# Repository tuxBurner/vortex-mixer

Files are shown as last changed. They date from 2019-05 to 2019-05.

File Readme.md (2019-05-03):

# Vortex Paint Mixer

This is my OpenSource vortex paint mixer.

You can also find it on thingiverse: https://www.thingiverse.com/thing:3605287

The reason why i created this, is i wanted to have an easy way to shake my paints. I used an adapter on a jig saw, which worked pretty well but was verry noisy to.

I stumpled over the vortex mixer from NDubiel on thingiverse: https://www.thingiverse.com/thing:534894 which was quite good but i wanted to improve some stuff.

Look the video how it works

Vortex Mixer in Action (http://www.youtube.com/watch?v=J79AnS1BsYA "Vortex Mixer in Action")

## Contribute

When you found a bug or have enhancement feel free to create a pull request or an issue :)

## Software used to create this project

* For 3d modelling: [http://openscad.org](http://openscad.org)
* For the pcb: [http://http://kicad-pcb.org/](http://kicad-pcb.org/)

I thank all the people which make it possible to create a project like this with there free software.

## Scad files

The case / lid and motorclamp scad file is the [scadfiles/case.scad](scadfiles/case.scad)

The top scad file is the [scadfiles/top.scad](scadfiles/top.scad)

## Howto build the mixer

### Tools

  * A 3d printer or use one of the services which print the objects for you
  * Soldering iron
  * Superglue
  * Hotglue gun
  * Optional if you want to create the pcb a mill or edging equipment

### Motorcontroller PCB Components

  * 1 x Diode (for example a 4007)
  * 1 x Poti 10K
  * 2 x Capacitor 47uF at 20V or greater 
  * 1 x LM317
  * 1 x Heatsink for the LM317 **required** 
  * 1 x 1k Resistor
  * 2 x Screw Terminal (Optional) 

### Other electronic Components

  * 12V DC Motor
  * Micro Switch
  * 1 x Powerplug (Optional) 
  * Poti Knob
  * 12 to 20 volt power supply

### General Components

  * 4 x Rubber Foot 
  * 1 x M3 * 30 Bolt + 3M Nut for the motor clamp
  * 5 x M3 tapping screws
  * Bearing for the cuppler
  * For the top 4M x 20 Bolt and 2 4M x Nuts

### Components to print

#### For the Mixer Case:

Print the following parts. Each one time.

I used 20% infill and PLA.

* [stls/case_bottom.stl](stls/case_bottom.stl)
* [stls/motor_clamp.stl](stls/motor_clamp.stl)
* [stls/wedge.stl](stls/wedge.stl)
* [stls/lid.stl](stls/lid.stl)
* [stls/coupler.stl](stls/coupler.stl)

#### For the paint bottle tops

Select the one which yo need.

I used 20% infill and PLA.

* [Vallejo](stls/tops/vallejo_top.stl)
* [Vallejo big bottle](stls/tops/vallejo_big_top.stl)
* [Games Workshop](stls/tops/games_workshop_top.stl)
* [Games Workshop old](stls/tops/games_workshop_old_top.stl)

## Motorcontroller PCB

The schemantics is like this

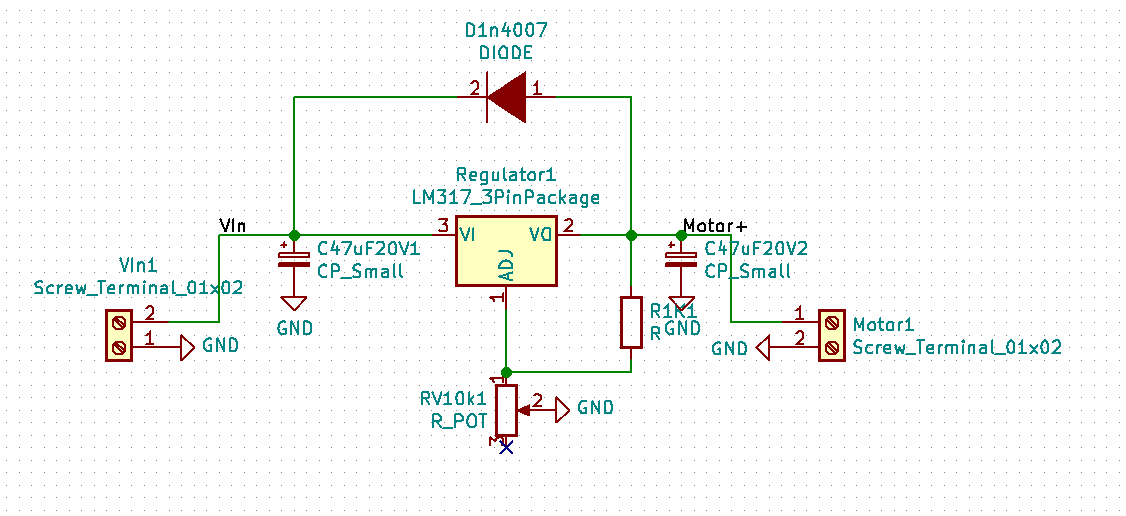
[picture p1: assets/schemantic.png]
PCB schemantic


You can either use the pcb which i generated with KICAD. The project files are located in the folder: **[pcb](pcb)**

If you don't have the possibility to create the pcb you can also freewire the electronics.

## Build Instructions

### Mixer

Hot glue the micro switch into the case and wire the switch to the power plug.







Put the motorclamp and the motor together


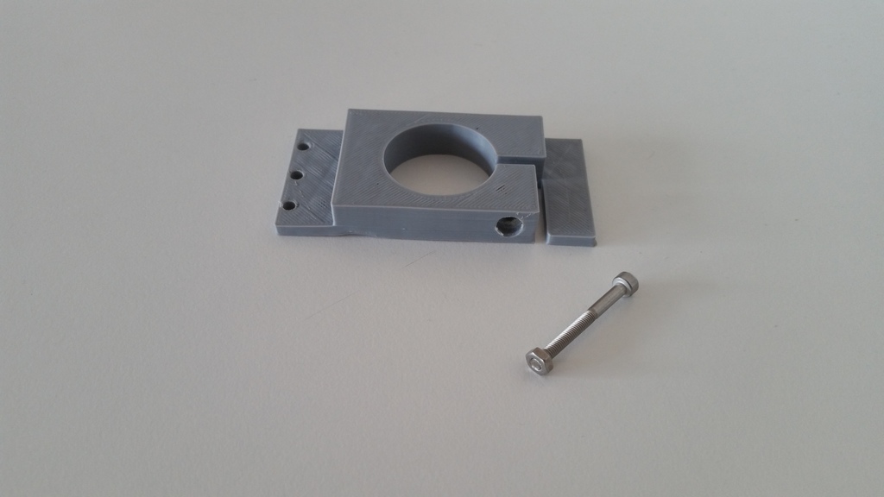
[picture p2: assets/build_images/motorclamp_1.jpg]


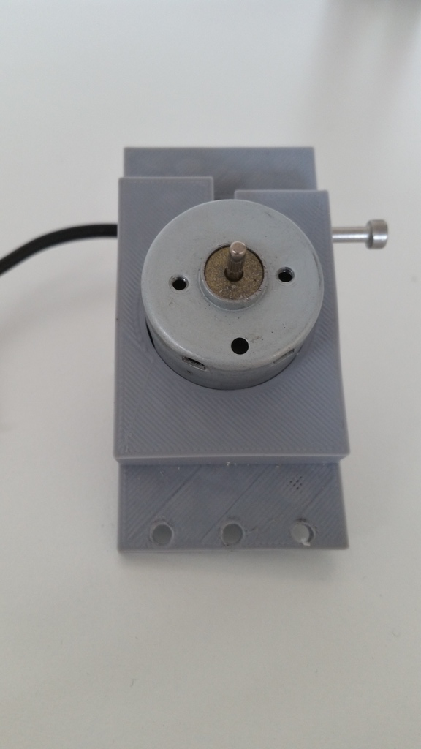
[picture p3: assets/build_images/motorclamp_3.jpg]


Assemble the pcb. Don't forget the heatsink :)



Wire the wires to the pcb from the powerplug, micro switch and the motor.



Fix the poti with the nut onto the case.

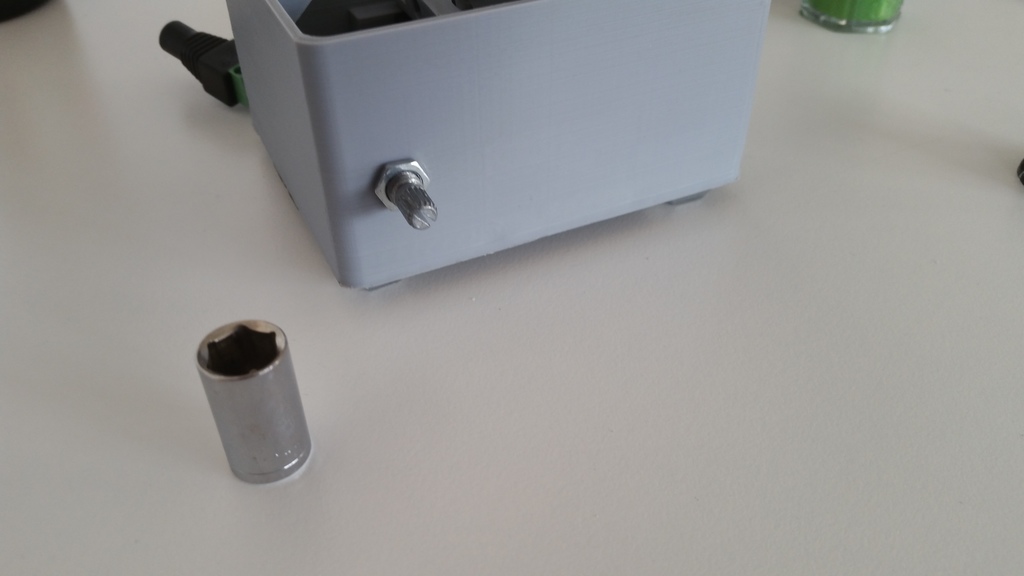
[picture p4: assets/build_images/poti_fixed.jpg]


Add the knob to the poti.

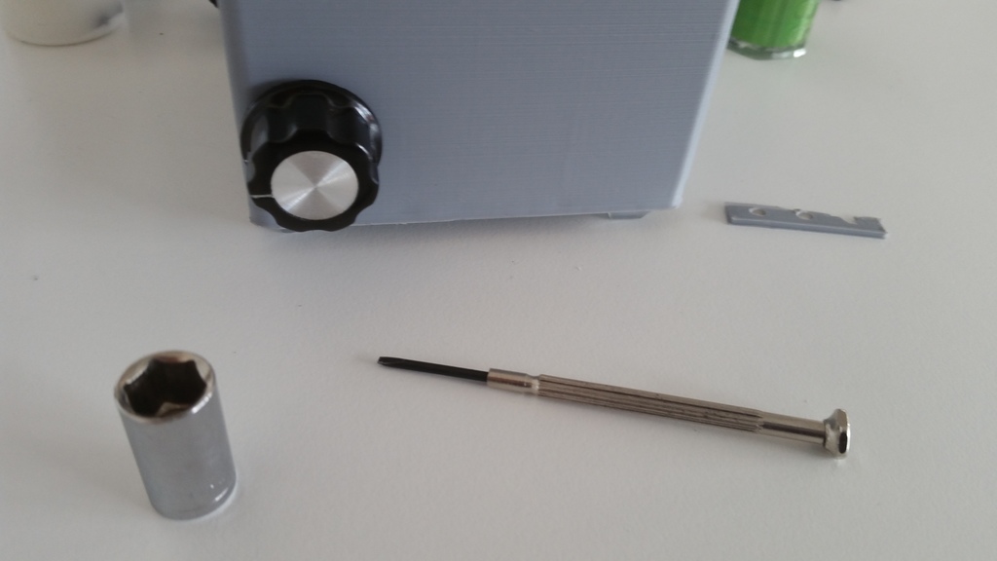
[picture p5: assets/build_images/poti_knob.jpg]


Add the wedge to the motor clamp. Mine broke a little bit when i tokked of the printer. But it is still working. 

¯\\_(ツ)_/¯

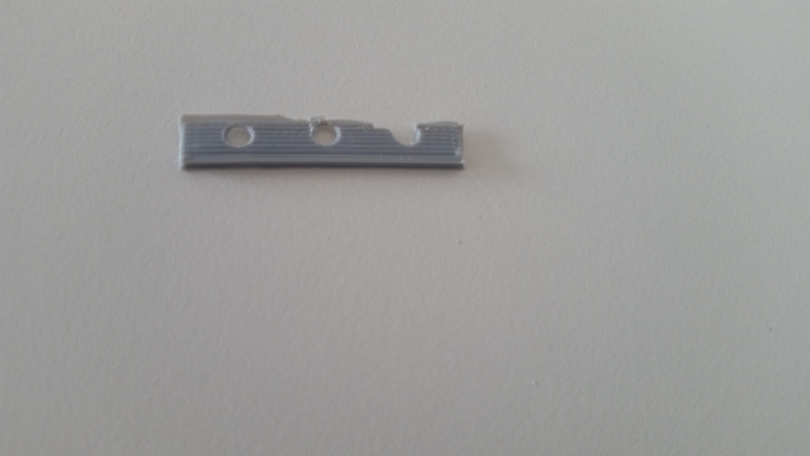
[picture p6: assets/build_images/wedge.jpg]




Screw the motorclamp into the case.



Screw the lid onto the case.



Superglue the bearing into the coupler.

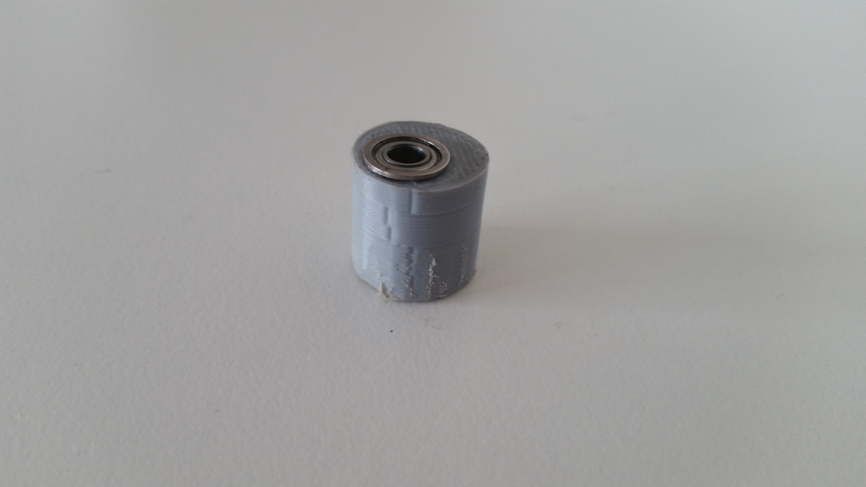
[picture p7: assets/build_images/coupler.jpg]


Put the coupler onto the motor.



## Paint bottle top

Here is a picture of the diffrent tops and the corresponding paint bottles.



Put a M4 nut into the bottom of the top.

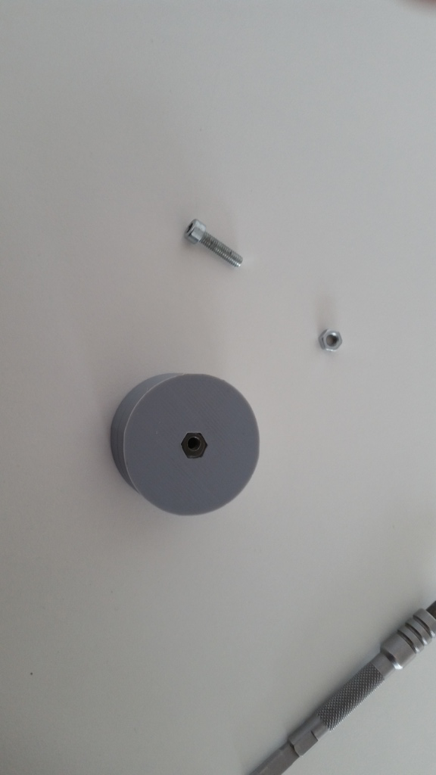
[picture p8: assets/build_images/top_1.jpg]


Screw a M4 bolt from the other side into the top and put a second M4 nut at the bottom. 

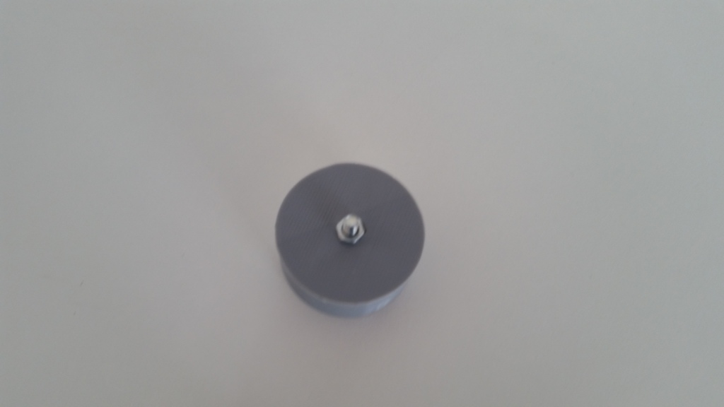
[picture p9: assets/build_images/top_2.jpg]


**DONE ! :)**

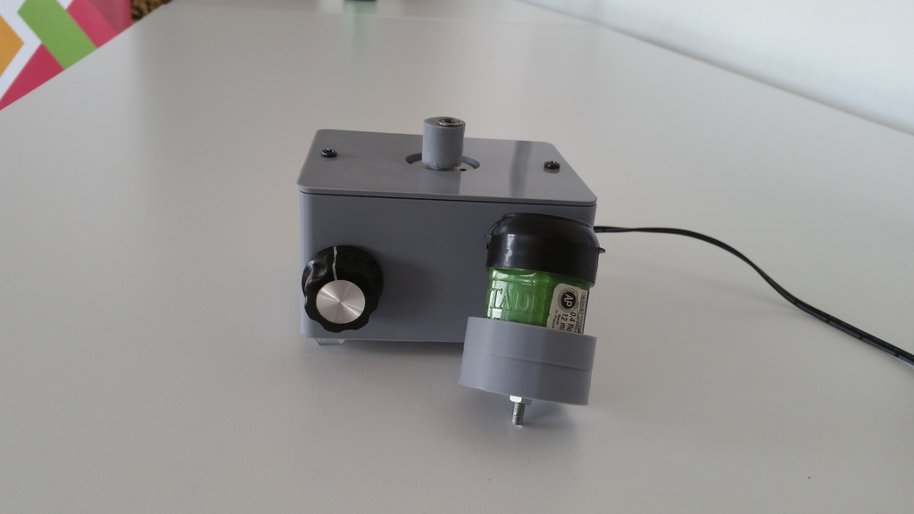
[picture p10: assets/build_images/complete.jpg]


Just plugin the power and push down the color top into the coupler.

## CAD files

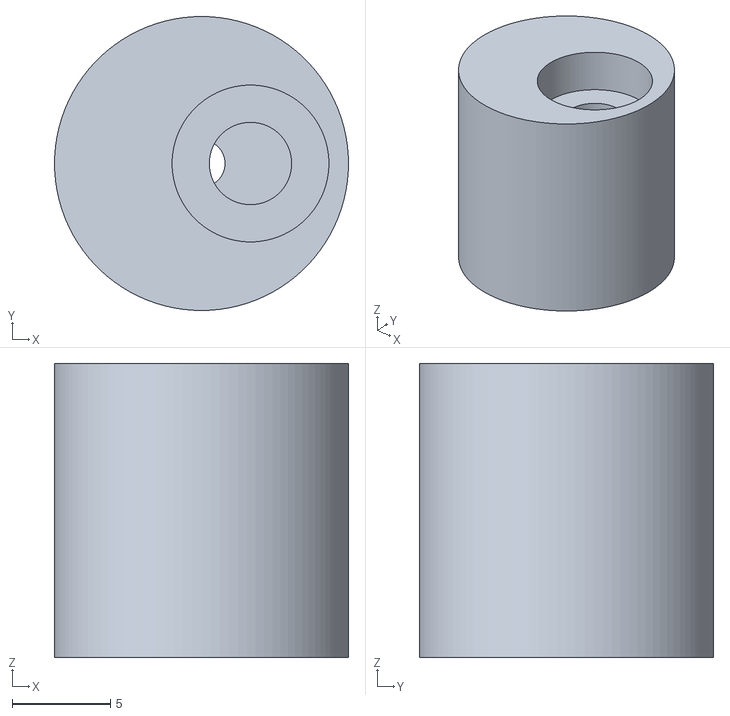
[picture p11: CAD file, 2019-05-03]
stls/coupler.stl
15.0 x 15.0 x 15.0

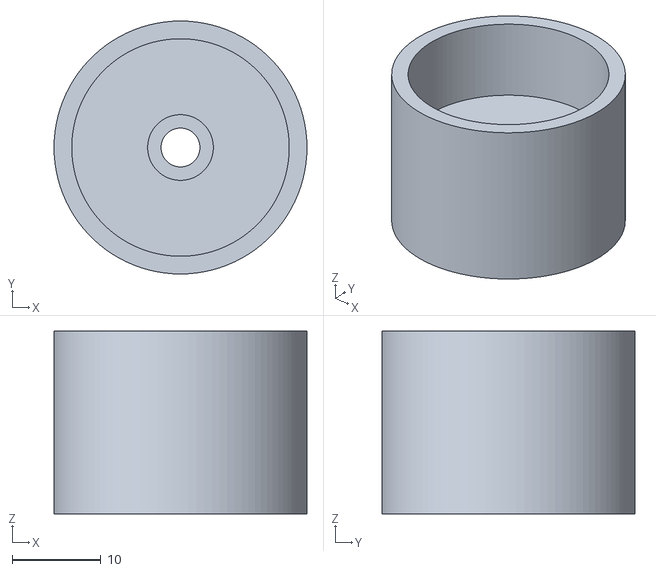
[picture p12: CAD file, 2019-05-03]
stls/tops/vallejo_top.stl
28.5 x 28.5 x 20.6

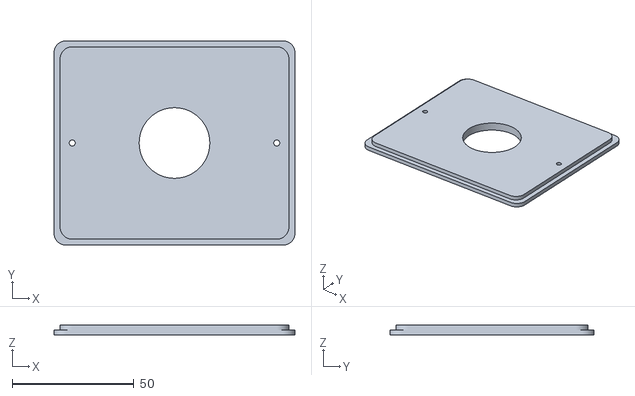
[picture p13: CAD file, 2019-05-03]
stls/lid.stl
99.0 x 84.0 x 4.00

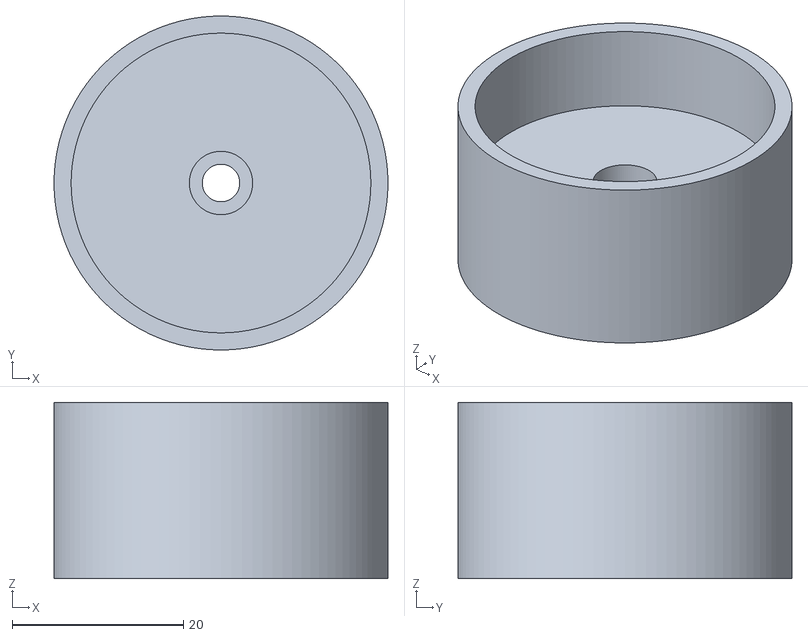
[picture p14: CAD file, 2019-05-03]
stls/tops/vallejo_big_top.stl
39.0 x 39.0 x 20.6

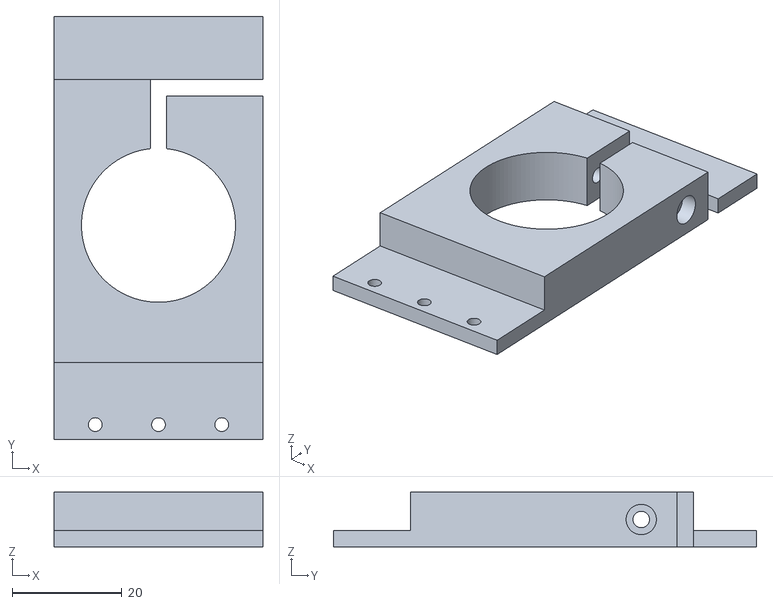
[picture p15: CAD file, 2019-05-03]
stls/motor_clamp.stl
38.0 x 77.0 x 10.0

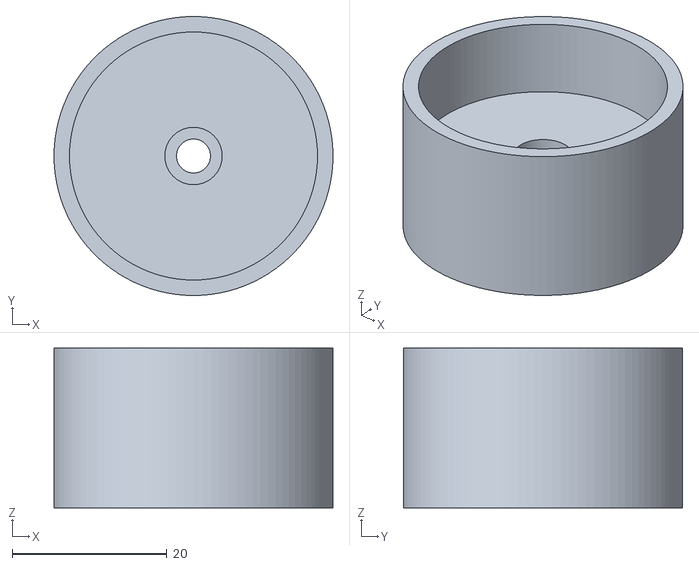
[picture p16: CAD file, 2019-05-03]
stls/tops/games_workshop_top.stl
36.0 x 36.0 x 20.6

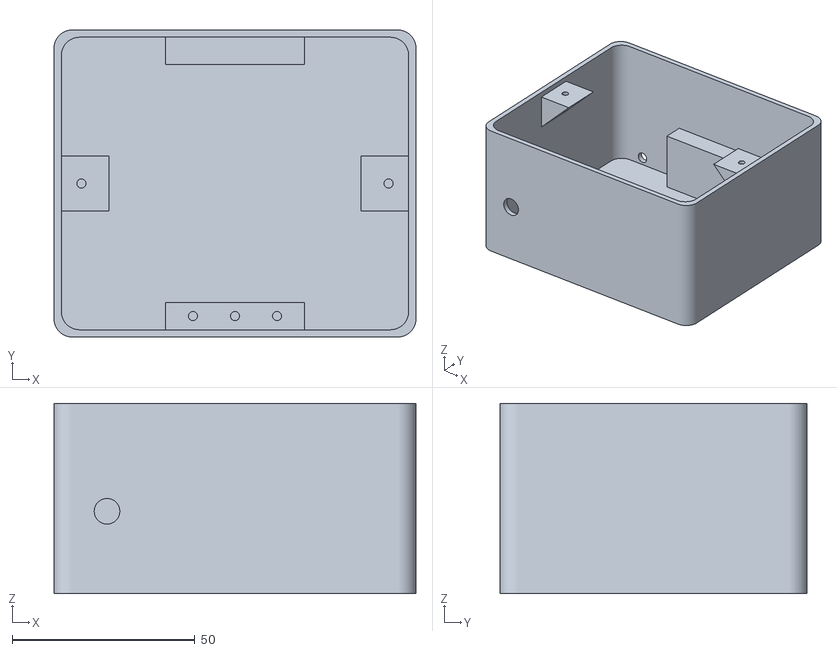
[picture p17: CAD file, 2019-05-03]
stls/case_bottom.stl
99.0 x 84.0 x 52.0

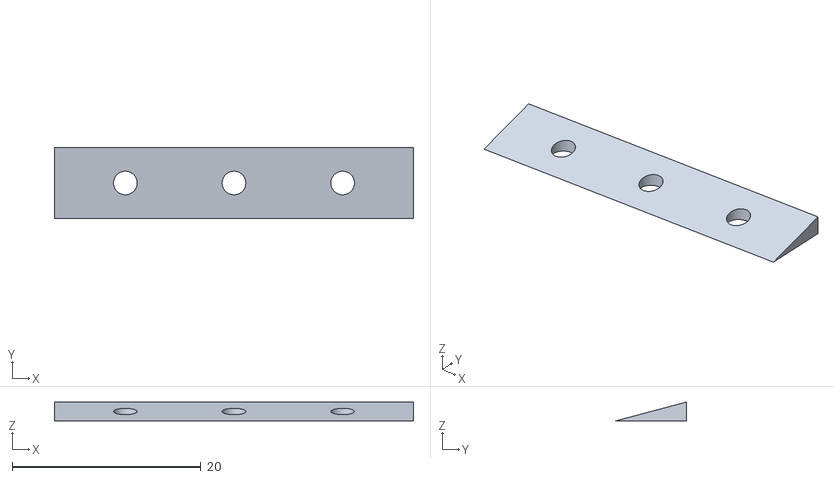
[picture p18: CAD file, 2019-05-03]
stls/wedge.stl
38.0 x 7.50 x 2.00

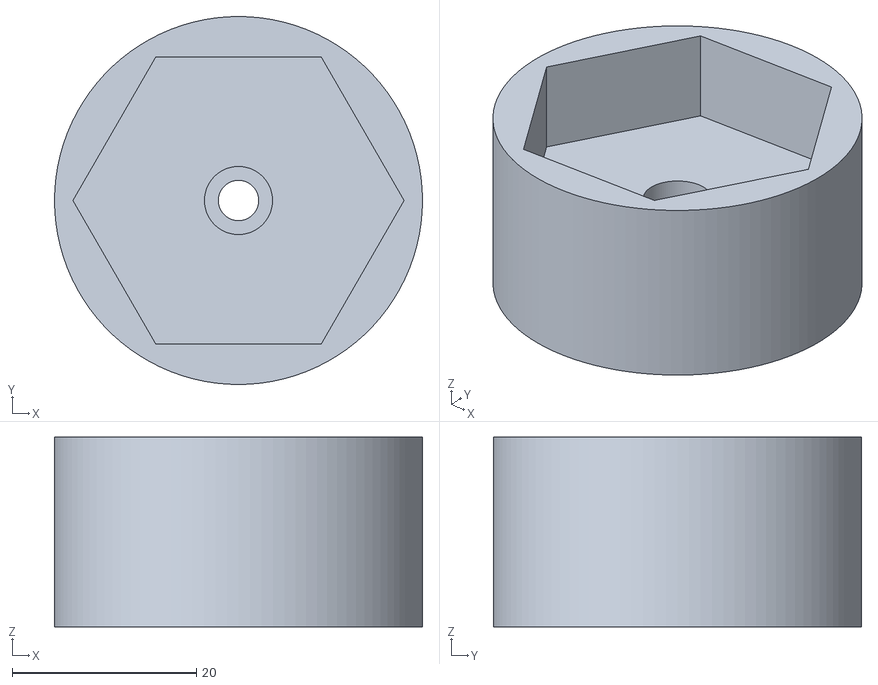
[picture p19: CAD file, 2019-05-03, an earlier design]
stls/tops/games_workshop_old_top.stl
40.0 x 40.0 x 20.6

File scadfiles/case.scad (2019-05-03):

use <boxes.scad>
include <nuts_and_bolts.scad>

/**
* Motor dimensions
*/
motorDia=28;
motorHeight=50;
motorShaftDia=3;
motorShaftLength=5;

/**
* Case dimensions
*/
caseWidth=95;
caseDepth=80;
caseHeight=motorHeight;
caseCornerRadius=5;

// thickness of the wall of the case
caseWallThickness=2;

/**
* Calculate the case real dimensions
*/
outerCaseWidth = caseWidth+2*caseWallThickness;
outerCaseDepth = caseDepth+2*caseWallThickness;
outerCaseHeight = caseHeight+caseWallThickness;

/**
* Case Lid dimensions
*/
caseLidLidHeight=2;
caseLidHeight=caseLidLidHeight*2;
caseLidTolerance=1;
caseLidScrewDia=2.5;

/**
* Prim for fixiatet the lid to the case
*/
caseLidFixPrismWidth=15;
caseLidFixPrismDepth=15;
caseLidFixPrismHeight=15;

/**
* Motor clamp dimensions
*/
motorClampHeight=10;
motorClampFlesh=5;
motorClampWidth=motorClampFlesh * 2 + motorDia;
motorClampLength = caseDepth - 2;
motorClampBoltSize=3;
motorClampNutHeight=motorClampWidth / 5;
motorClampTolerance=3;
motorClampLidLength=caseDepth / 8;
motorClampFixHeight=3;
motorClampFixWidth=15;
motorClampFixTolerance=1;
motorClampWedgeHeight=2;

motorClampCaseFixHeight =  caseHeight / 2;
motorClampCaseFixDepth = motorClampFixWidth / 2;

/**
* Motor clamp variables where to put the screws for the motorclamp and the case
*/
motorClampFixScrewDia = 2.5;
motorClampFixScrewHeight = 10;
motorClampFixScrewTolerance = 5 + motorClampFixScrewDia;
motorClampFixScrewPositions=[
  [motorClampFixScrewTolerance, motorClampCaseFixDepth / 2],
  [motorClampWidth / 2, motorClampCaseFixDepth / 2],
  [motorClampWidth - motorClampFixScrewTolerance, motorClampCaseFixDepth / 2],
];

/**
* Dimensions where to put the micro switch at
*/
microSwitchCaseFixHeight = motorClampCaseFixHeight - 2;
microSwitchCaseFixDepth = motorClampCaseFixDepth;


/**
* For debug purpose the pcb 
*/
pcbXTollerance=1;
pcbWidth=24;
pcbDepth=33;
pcbHeight=24;

/**
* Poti dimensions
*/
potiHoleDia=7;
potiHoleXOffset=8;
potiHolezOffset=17;

/**
* Diameter for the power cable
*/
cableHoleDia=4;

/**
* Coupler dimensions
*/
couplerDia=15;
couplerHeight=15;
couplerScrewDia=4.2;
couplerBearingDia=8;
couplerBearingHeight=3;
couplerMoterShaftDia=2.4;
couplerBearingOffset=2.5;


$fn=100;


$previewMotor=false;
$debugLid=false;
$debugMotorClamp=false;



/**
* Generates the bottom of the case
*/
module bottomCase() {  
  union() {
    translate([outerCaseWidth / 2, outerCaseDepth / 2, outerCaseHeight / 2]) {
      difference() {  
        roundedBox([outerCaseWidth, outerCaseDepth, outerCaseHeight], caseCornerRadius, true);
        translate([0, 0, caseWallThickness]) {
          roundedBox([caseWidth, caseDepth, caseHeight], caseCornerRadius, true);
        }
      }
    }

    translate([0, 0, outerCaseHeight -caseLidFixPrismHeight-caseLidLidHeight]) {
      translate([0, (outerCaseDepth - caseLidFixPrismWidth) / 2, 0]) {
        lidHolder(caseLidFixPrismWidth, caseLidFixPrismHeight, caseLidFixPrismDepth);  
      }
      translate([outerCaseWidth , (outerCaseDepth + caseLidFixPrismWidth) / 2, 0]) {
        rotate([0, 0, 180]) {      
          lidHolder(caseLidFixPrismWidth, caseLidFixPrismHeight, caseLidFixPrismDepth);  
        }
      }
      translate([(outerCaseWidth + caseLidFixPrismWidth) / 2 ,0, 0]) {
        rotate([0, 0, 90]) {      
         // #lidHolder(caseLidFixPrismWidth, caseLidFixPrismHeight, caseLidFixPrismDepth);  
        }
      }
      translate([(outerCaseWidth - caseLidFixPrismWidth) / 2 ,outerCaseDepth, 0]) {
        rotate([0, 0, -90]) {      
          //lidHolder(caseLidFixPrismWidth, caseLidFixPrismHeight, caseLidFixPrismDepth);  
        }
      }
    }
  
    translate([(outerCaseWidth - motorClampWidth) / 2 , caseWallThickness,caseWallThickness]) {    
      motorClampCaseFixiation();    
      translate([0,caseDepth - microSwitchCaseFixDepth, 0]) {
        microSwitchHolder();  
      }
    }
  }
}

/**
* Draws the motor clamp
*/
module motorClamp() {
  color("DarkKhaki") {
    difference() {
      cube(size=[motorClampWidth, motorClampLength, motorClampHeight], center=false);
      
      // cut out the fixiation which is thinner so we can bend it down
      translate([0, 0, motorClampFixHeight]) {
        cube(size=[motorClampWidth, motorClampFixWidth,motorClampHeight- motorClampFixHeight], center=false);  
      }

      // cut off the tolerance      
      cube(size=[motorClampWidth, motorClampFixTolerance, motorClampFixHeight], center=false);
      

      // cut out the screwholes
      clampScrewHoles(motorClampFixHeight);
   
      // cut out the motor
      translate([motorClampWidth / 2, caseDepth / 2, 0]) {
        cylinder(d=motorDia, h=motorClampHeight, center=false);  
      }

      // cut out the tolerance slit 
      motorClampLidOffset = (caseDepth + motorDia) / 2 -0.5;
      translate([(motorClampWidth - motorClampTolerance) / 2,motorClampLidOffset , 0]) {
        cube(size=[motorClampTolerance, motorClampLidLength, motorClampHeight], center=false);  
        translate([0, motorClampLidLength, 0]) {
          cube(size=[motorClampWidth - motorClampTolerance, motorClampTolerance, motorClampHeight], center=false);  
        }
      } 
      
      // add the hole for the fixiation screw
      translate([motorClampWidth - motorClampBoltSize , (motorClampLength - motorClampBoltSize * 2 - (motorClampLength / 2 - motorDia / 2 - motorClampLidLength)), motorClampHeight  / 2]) { 
        rotate([0, 270, 0]) {
          boltHole(motorClampBoltSize, length= motorClampWidth-motorClampBoltSize, proj=-1);  
        }        
      } 

      // add a nut hole 
      translate([motorClampNutHeight, (motorClampLength - motorClampBoltSize * 2 - (motorClampLength / 2 - motorDia / 2 - motorClampLidLength)), motorClampHeight  / 2]) {         
        rotate([0, 270, 0]) {
          cylinder(r= METRIC_NUT_AC_WIDTHS[motorClampBoltSize]/2+0.5, h=motorClampNutHeight, $fn = 6, center=[0,0]);
        }
      }

      // slim the end of the clamp 
      backCutOffOffset = motorClampLidOffset + motorClampLidLength + motorClampTolerance;
      translate([0, backCutOffOffset, motorClampFixHeight]) {
        cube(size=[motorClampWidth, motorClampLength - backCutOffOffset, motorClampHeight- motorClampFixHeight], center=false);
      }
    }
  }
}

/**
* Cut out the screwholes for fix the clamp
*/ 
module clampScrewHoles(holesHeight) {
  for(screwPos = motorClampFixScrewPositions) {
    translate([screwPos[0], screwPos[1], 0]) {
      cylinder(d=motorClampFixScrewDia, h=holesHeight, center=false);  
    }
  }
}

/**
* Draws the clamp case motor fixiation
*/
module motorClampCaseFixiation() {
  color("Teal") {
    difference() {
      cube(size=[motorClampWidth, motorClampCaseFixDepth, motorClampCaseFixHeight], center=false);
      translate([0, 0, motorClampCaseFixHeight - motorClampFixScrewHeight]) {
        clampScrewHoles(motorClampFixScrewHeight); 
      }    
    }
  }
}

/**
* Draws the holder for the microswitch
*/
module microSwitchHolder() {
  color("Gainsboro") {
    difference() {
      cube(size=[motorClampWidth, microSwitchCaseFixDepth, microSwitchCaseFixHeight], center=false);      
    }
  }
}

/**
* Draws the lid
*/
module lid() {
  translate([outerCaseWidth / 2, outerCaseDepth / 2, 0]) {
    difference() {
      union() {
        roundedBox([outerCaseWidth, outerCaseDepth, caseLidHeight - caseLidLidHeight], caseCornerRadius, true);
        translate([0, 0, caseLidLidHeight]) {
          roundedBox([caseWidth - caseLidTolerance, caseDepth- caseLidTolerance, caseLidLidHeight], caseCornerRadius, true);
        }
      }
  
      translate([0, 0, -1 * (caseLidLidHeight / 2)]) {
        cylinder(d=motorDia + caseLidTolerance, h=caseLidHeight, center=false);  
        
        translate([(outerCaseWidth - caseLidFixPrismDepth) / 2, 0, 0]) {
          cylinder(d=caseLidScrewDia, h=caseLidHeight, center=false);  
        }

        translate([-1*(outerCaseWidth - caseLidFixPrismDepth) / 2, 0, 0]) {
          cylinder(d=caseLidScrewDia, h=caseLidHeight, center=false);  
        }

        translate([0,-1*(outerCaseDepth - caseLidFixPrismDepth) / 2, 0]) {
         // cylinder(d=caseLidScrewDia, h=caseLidHeight, center=false);  
        }

        translate([0,(outerCaseDepth - caseLidFixPrismDepth) / 2, 0]) {
          //cylinder(d=caseLidScrewDia, h=caseLidHeight, center=false);  
        }
        
      }
    }
  }
}

/**
* In preview mode this is drawn to check if the pcb fits into the case
*/
module pcbPreview() {
  color("Red") {
    translate([caseWallThickness + pcbXTollerance, caseWallThickness, caseWallThickness]) {
     cube(size=[pcbWidth, pcbDepth, pcbHeight], center=false);   
    }    
  }
}
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

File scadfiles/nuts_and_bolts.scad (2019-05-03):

// Copyright 2010 D1plo1d

// This library is dual licensed under the GPL 3.0 and the GNU Lesser General Public License as per http://creativecommons.org/licenses/LGPL/2.1/ .

//testNutsAndBolts();

module SKIPtestNutsAndBolts()
{
	$fn = 360;
	translate([0,15])nutHole(3, proj=2);
	boltHole(3, length= 30, proj=2);
}

MM = "mm";
INCH = "inch"; //Not yet supported

//Based on: http://www.roymech.co.uk/Useful_Tables/Screws/Hex_Screws.htm
METRIC_NUT_AC_WIDTHS =
[
	-1, //0 index is not used but reduces computation
	-1,
	4.38,//m2
	6.40,//m3
	8.10,//m4
	9.20,//m5
	11.50,//m6
	-1,
	15.00,//m8
	-1,
	19.60,//m10
	-1,
	22.10,//m12
	-1,
	-1,
	-1,
	27.70,//m16
	-1,
	-1,
	-1,
	34.60,//m20
	-1,
	-1,
	-1,
	41.60,//m24
	-1,
	-1,
	-1,
	-1,
	-1,
	53.1,//m30
	-1,
	-1,
	-1,
	-1,
	-1,
	63.5//m36
];
METRIC_NUT_THICKNESS =
[
	-1, //0 index is not used but reduces computation
	-1,
	1.6,//m2
	2.40,//m3
	3.20,//m4
	4.00,//m5
	5.00,//m6
	-1,
	6.50,//m8
	-1,
	8.00,//m10
	-1,
	10.00,//m12
	-1,
	-1,
	-1,
	13.00,//m16
	-1,
	-1,
	-1,
	16.00//m20
	-1,
	-1,
	-1,
	19.00,//m24
	-1,
	-1,
	-1,
	-1,
	-1,
	24.00,//m30
	-1,
	-1,
	-1,
	-1,
	-1,
	29.00//m36
];

COURSE_METRIC_BOLT_MAJOR_THREAD_DIAMETERS =
[//based on max values
	-1, //0 index is not used but reduces computation
	-1,
	1.6,//m2
	2.98,//m3
	3.978,//m4
	4.976,//m5
	5.974,//m6
	-1,
	7.972,//m8
	-1,
	9.968,//m10
	-1,
	11.966,//m12
	-1,
	-1,
	-1,
	15.962,//m16
	-1,
	-1,
	-1,
	19.958,//m20
	-1,
	-1,
	-1,
	23.952,//m24
	-1,
	-1,
	-1,
	-1,
	-1,
	29.947,//m30
	-1,
	-1,
	-1,
	-1,
	-1,
	35.940//m36
];

//Based on: http://www.roymech.co.uk/Useful_Tables/Screws/cap_screws.htm
METRIC_BOLT_CAP_DIAMETERS =
[
	-1, //0 index is not used but reduces computation
	-1,
	-1,
	5.50,//m3
	7.00,//m4
	8.50,//m5
	10.00,//m6
	-1,
	13.00,//m8
	-1,
	16.00,//m10
	-1,
	18.00,//m12
	-1,
	-1,
	-1,
	24.00,//m16
	-1,
	-1,
	-1,
	30.00//m20
	-1,
	-1,
	-1,
	36.00,//m24
	-1,
	-1,
	-1,
	-1,
	-1,
	45.00,//m30
	-1,
	-1,
	-1,
	-1,
	-1,
	54.00//m36
];

module nutHole(size, units=MM, tolerance = +0.0001, proj = -1)
{
	//takes a metric screw/nut size and looksup nut dimensions
	radius = METRIC_NUT_AC_WIDTHS[size]/2+tolerance;
	height = METRIC_NUT_THICKNESS[size]+tolerance;
	if (proj == -1)
	{
		cylinder(r= radius, h=height, $fn = 6, center=[0,0]);
	}
	if (proj == 1)
	{
		circle(r= radius, $fn = 6);
	}
	if (proj == 2)
	{
		translate([-radius/2, 0])
			square([radius*2, height]);
	}
}

module boltHole(size, units=MM, length, tolerance = +0.0001, proj = -1)
{
	radius = COURSE_METRIC_BOLT_MAJOR_THREAD_DIAMETERS[size]/2+tolerance;
	capHeight = size+tolerance;
	capRadius = METRIC_BOLT_CAP_DIAMETERS[size]/2+tolerance;

	if (proj == -1)
	{
	translate([0, 0, -capHeight])
		cylinder(r= capRadius, h=capHeight);
	cylinder(r = radius, h = length);
	}
	if (proj == 1)
	{
		circle(r = radius);
	}
	if (proj == 2)
	{
		translate([-capRadius/2, -capHeight])
			square([capRadius*2, capHeight]);
		square([radius*2, length]);
	}
}

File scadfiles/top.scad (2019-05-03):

include <nuts_and_bolts.scad>

/**
* Size of the bolts
*/
boltSize=4;
boltTolerance=0.2;
boltFlesh=3;

bottomHeight = boltSize + boltTolerance + boltFlesh + METRIC_NUT_THICKNESS[boltSize] + boltTolerance;

wallThickness=2;

$fn=100;

/**
* Top configurations
*/
topConfigurations = [
  [10, 24.5], // normal vallejo top
  [10, 35], // vallejo big top
  [10,32], // games workshop 
  [10,36,6] // games workshop old
];



/**
* Module for creating a top
*/
module top(height, dia, fn=100) {
  
  union() {
    difference() {
      cylinder(d=dia+2*wallThickness, h=bottomHeight, center=false);
      translate([0, 0, bottomHeight - boltSize - boltTolerance]) {
        rotate([0, 180, 0]) {
          #boltHole(size=boltSize,length=bottomHeight, tolerance=boltTolerance);  
        }  
      }
      nutHole(size=boltSize,tolerance=boltTolerance);    
    }
  
    translate([0, 0, bottomHeight]) {
      difference() {
        cylinder(d=dia+2*wallThickness, h=height, center=false);
        cylinder(d=dia, h=height, center=false,$fn=fn);
      }
    }
  }
}


/**
* Iterate over the tops and draw them
*/
for(idx = [0:len(topConfigurations)-1])  {  
  xOffset = sumv(topConfigurations,idx,0);
  translate([xOffset,0,0]) {
    fn = (len(topConfigurations[idx]) == 2) ? 100 : topConfigurations[idx][2];     
    top(height = topConfigurations[idx][0], dia = topConfigurations[idx][1], fn = fn);
  }
}

/**
* Used to calculate the sum of all dias from to
*/
function sumv(v,i,s=0) = (i==s ? v[i][1]+10 : v[i][1]+10 + sumv(v,i-1,s));

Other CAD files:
scadfiles/boxes.scad

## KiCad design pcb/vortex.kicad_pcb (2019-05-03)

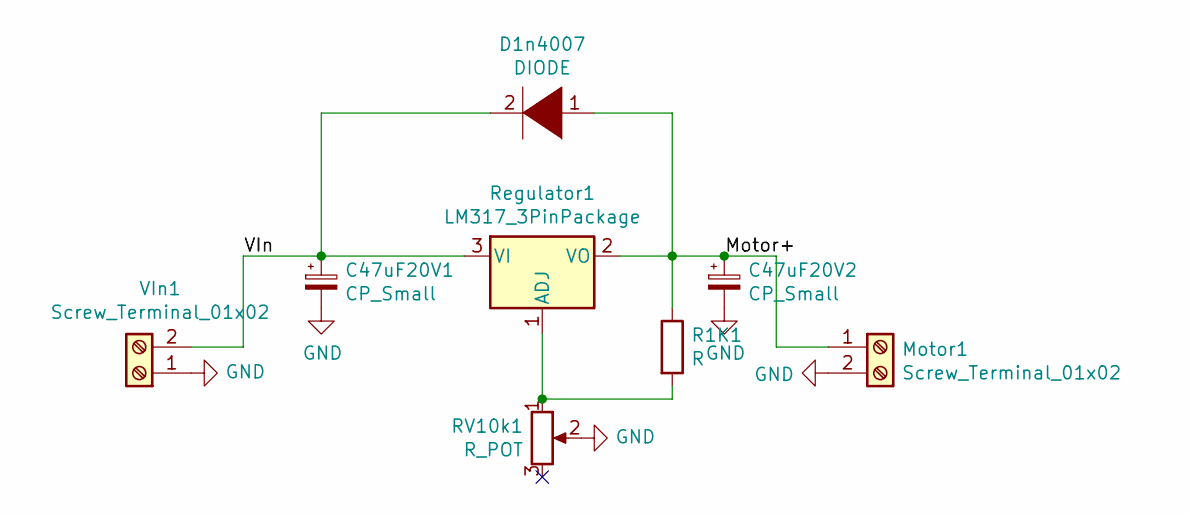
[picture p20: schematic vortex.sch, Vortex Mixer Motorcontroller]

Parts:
C47uF20V1, C47uF20V2: CP_Small; CP_Radial_D5.0mm_P2.50mm
D1n4007: DIODE; D_A-405_P7.62mm_Horizontal
Motor1: Screw_Terminal_01x02; TerminalBlock_bornier-2_P5.08mm
R1K1: R; R_Axial_DIN0207_L6.3mm_D2.5mm_P7.62mm_Horizontal
RV10k1: R_POT; Potentiometer_Alps_RK163_Single_Horizontal
Regulator1: LM317_3PinPackage; TO-220-3_Vertical
VIn1: Screw_Terminal_01x02; TerminalBlock_bornier-2_P5.08mm

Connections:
/Motor+: C47uF20V2.1, D1n4007.1 (K), Motor1.1, R1K1.1, Regulator1.2 (VO)
/VIn: C47uF20V1.1, D1n4007.2 (A), Regulator1.3 (VI), VIn1.2
GND: C47uF20V1.2, C47uF20V2.2, Motor1.2, RV10k1.2, VIn1.1
unnamed: R1K1.2, RV10k1.1, Regulator1.1 (ADJ)

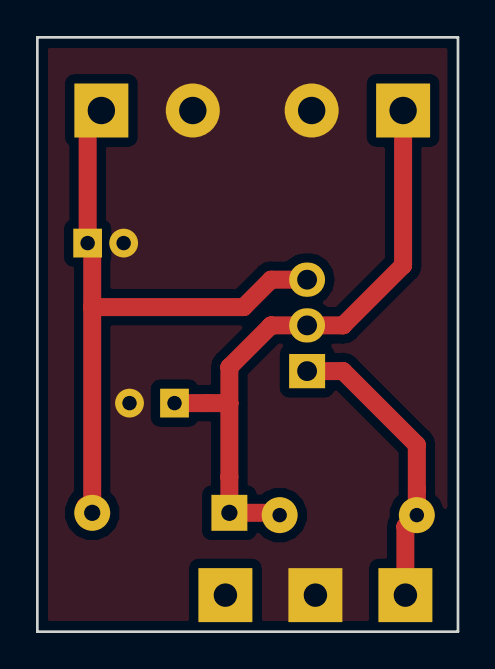
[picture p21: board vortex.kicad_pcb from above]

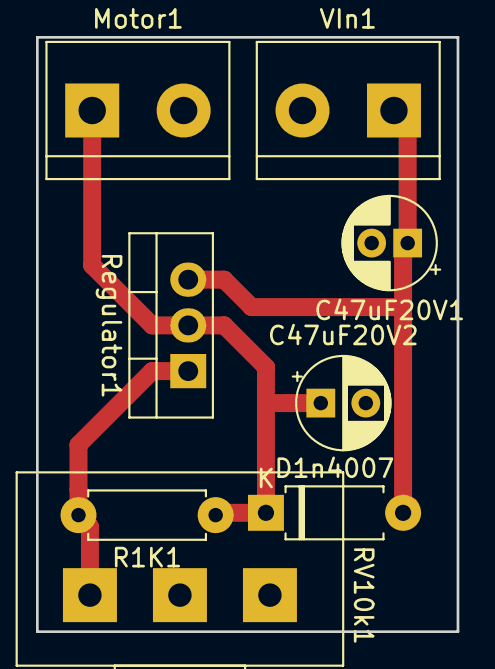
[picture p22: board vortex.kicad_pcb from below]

Board: 2 copper layers, 23.4 x 33.0 mm, 8 parts (8 on the bottom side), 4 nets.

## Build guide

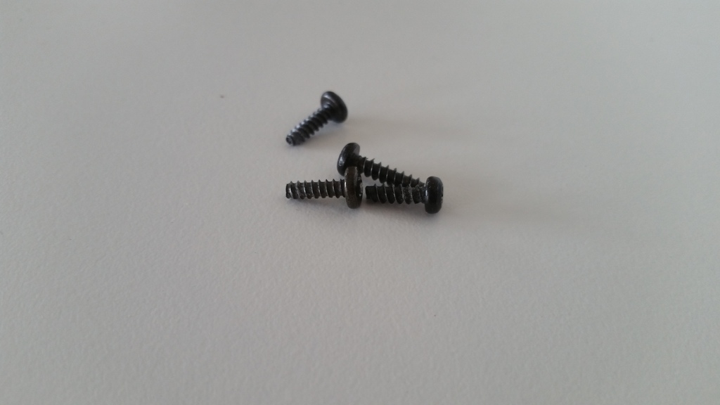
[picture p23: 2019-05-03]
assets/build_images/tappingscrews.jpg
